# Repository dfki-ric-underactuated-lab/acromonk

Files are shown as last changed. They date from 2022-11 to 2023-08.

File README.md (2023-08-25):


<div align="center">

# AcroMonk: A Minimalist Underactuated Brachiating Robot
</div>

<div align="center">
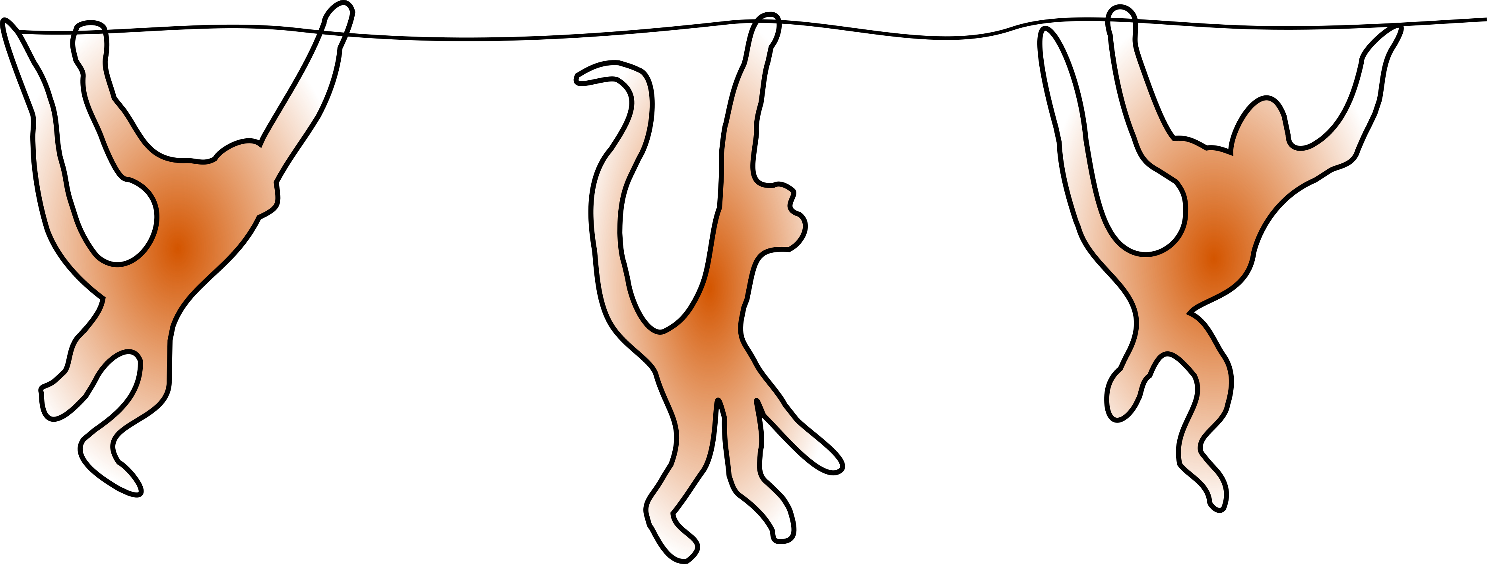
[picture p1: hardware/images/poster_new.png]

</div>

<div align="center">

</div>

## Description
This project offers an open-source and low-cost kit to test control algorithms
for underactuated robots.
it implements a **brachiation robot** platform called **AcroMonk** which
can brachiate robustly over a horizontally laid ladder bar. AcroMonk is
the simplest possible underactuated brachiator built using one quasi-direct
drive actuator (QDD) and passive grippers. This is the first brachiator with
unactuated grippers that can perform more than two brachiation maneuvers.
This project offers different control methods for trajectory stabilization
which can be studied using the kit. Additionally, it provides a list of
components, discusses best practices for implementation, and presents results
from experiments with the simulator and the real system. This repository
describes the hardware (CAD, Bill Of Materials ([BOM](hardware/bills-of-materials.md)) etc.) required to build
the physical system and provides the software (URDF models, simulation and controllers) to control it.

## Paper and Video References

The work is published in IEEE Robotics and Automation Letters 2023. The hardware experiment video of AcroMonk is also featured as an awesome robot video in [IEEE Spectrum Video Friday](https://spectrum.ieee.org/video-friday-acromonk).

Further links:
* Paper is available on [IEEE](https://ieeexplore.ieee.org/document/10106397) and [arXiv](https://arxiv.org/abs/2305.08373).
* Video is available on [youtube](https://youtu.be/FIcDNtJo9Jc).
## Documentation

The dynamics of the AcroMonk is explained [here](hardware/acrm-equations.md). Additionally, [mechatronics design](hardware/testbench-description.md), [behavior generation](software/python/simulation/behavior_generation/README.md) and [control](software/python/simulation/behavior_control/README.md) for the continuous brachiation are described in their respective readme files.

* [Mechatronics Design](hardware/testbench-description.md)
* [Behavior Generation](software/python/simulation/behavior_generation/README.md)
* [Behavior Control](software/python/simulation/behavior_control/README.md)
* [Software Guide](software/python/README.md)
* [Bill Of Materials (BOM)](hardware/bills-of-materials.md)

The CAD file is also provided on grabCAD.com. You can use the 3D viewer from their website to display the 3D model directly within your browser.
 - [Display AcroMonk in 3D](https://grabcad.com/library/acromonk-1)
## Authors #

* [Shivesh Kumar](https://robotik.dfki-bremen.de/en/about-us/staff/person/shku02) (Project Supervisor)
* [Mahdi Javadi](https://robotik.dfki-bremen.de/en/about-us/staff/person/maja04) (Hardware and Software Maintainer, Trajectory Optimization and Stabilization)
* [Daniel Harnack](https://robotik.dfki-bremen.de/en/about-us/staff/daha03.html) (Software Maintainer, Reinforcement Learning)
* [Shubham Vyas](https://robotik.dfki-bremen.de/en/about-us/staff/person/shvy01) (Trajectory Optimization, Hardware Concept)
* [Daniel Pizzutilo](https://robotik.dfki-bremen.de/de/ueber-uns/mitarbeiter/dapi01) (Mechatronics Design)
* Paula Stocco (Trajectory Optimization and Stabilization)

Feel free to contact us if you have questions about the test bench. Enjoy!

## Contributing

1. Fork it (<https://github.com/yourname/yourproject/fork>)
2. Create your feature branch (`git checkout -b feature/fooBar`)
3. Commit your changes (`git commit -am 'Add some fooBar'`)
4. Push to the branch (`git push origin feature/fooBar`)
5. Create a new Pull Request

## Safety Notes #

When working with a real system be careful and mind the following safety measures:

* Brushless motors can be very powerful, moving with tremendous force and speed. Always limit the range of motion, power, force and speed using configurable parameters, currently limited supplies, and mechanical design.

* The robot must be placed in a ladder bar cage and kept at least one-meter distance from the acromonk in case of operation.

* Make sure you have access to an emergency stop while doing experiments. Be extra careful while operating in the pure torque control loop.

* The robot is equipped with an onboard Lithium Polymer battery and needs proper care and attention. Make sure that you have all the necessary information for the LiPo batteries.

## Acknowledgments #
This work has been performed in the M-RoCK project funded by the
German Aerospace Center (DLR) with federal funds (Grant Number: FKZ 01IW21002)
from the Federal Ministry of Education and Research (BMBF) and is additionally
supported with project funds from the federal state of Bremen for setting up
the Underactuated Robotics Lab (Grant Number: 201-342-04-2/2021-4-1). The fourth author acknowledges support from the Stardust Reloaded project which has received funding from the European Union’s Horizon 2020 research and innovation program under the Marie Skłodowska-Curie grant agreement No 813644.
<div align="center">

</div>

## License

This work has been released under the BSD 3-Clause License. Details and terms of use are specified in the LICENSE file within this repository. Note that we do not publish third-party software, hence software packages from other developers are released under their very own terms and conditions, e.g. Stable baselines (MIT License) and Tensorflow (Apache License v2.0). If you install third-party software packages along with this repo ensure that you follow each individual license agreement.

## Citation

1. Javadi M., Harnack D., Stocco P., Kumar S., Vyas S., Pizzutilo D., Kirchner F., (2022). AcroMonk: A Minimalist Underactuated Brachiating Robot. In: IEEE Robotics and Automation Letters (RA-L), vol. 8, no. 6, pp. 3637-3644, June 2023, doi: 10.1109/LRA.2023.3269296.
```
@ARTICLE{10106397,
  author={Javadi, Mahdi and Harnack, Daniel and Stocco, Paula and Kumar, Shivesh and Vyas, Shubham and Pizzutilo, Daniel and Kirchner, Frank},
  journal={IEEE Robotics and Automation Letters}, 
  title={AcroMonk: A Minimalist Underactuated Brachiating Robot}, 
  year={2023},
  volume={8},
  number={6},
  pages={3637-3644},
  doi={10.1109/LRA.2023.3269296}}
```

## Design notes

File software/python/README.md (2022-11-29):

<div align="center">

# Software guide
</div>

This document provides instruction guides on executions of the software package in simulation and on the Raspberry Pi for real-time execution.

- [Simulation guide](simulation/README.md)
- [AcroMonk system guide](real_system/README.md)

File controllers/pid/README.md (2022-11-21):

#  Proportional–Integral–Derivative (PID) Control #

## Theory #

This controller is designed to follow a precomputed trajectory. Particulary, the controller can process trajectories that have been found with help of the [trajectory optimization](../../trajectory_optimization/direct_collocation/README.md). The torque processed by the PID control terms via:
```math
u(t) = K_p e(t) + K_i \int_0^t e(t') \text{d}t' + K_d \frac{\text{d}e(t)}{\text{d}t}
```
where $`e(t)`$ is the position error at timestep t. The values are assumed to be in SI units, i.e. time in s, position in rad, velocity in rad/s, torque in Nm.

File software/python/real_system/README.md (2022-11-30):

# Trajectory Stabilization with AcroMonk
The following instructions assume that the scripts will be executed on the Raspberry Pi. The required packages that need to be installed on the Raspberry Pi are provided in the [requirement.txt](requirements.txt).

A Makefile is provided in the following folder for the automatic execution of the robust forward brachiation using TVLQR and PD controller:

`software/python/real_system/Makefile`

The following parameters can be used for arbitrary behavior:

```
TEST          : stabilizing controller (pd, tvlqr), default=pd
FILE          : swing trajectory (BF trajectory in data/trajectories/closed_loop folder), default=BF_tvlqr.csv
MOTOR_ID      : mjbots servo id, default=7
BUS_NUMBER    : bus number on pi3hat, default=4
FILE_RECOVERY : recovery trajectory (Recovery trajectory in data/trajectories/closed_loop folder), default=ZF_tvlqr.csv
INIT_CONF     : initial configuration of the AcroMonk (1, 2), default=1: description provided in initial configuration section of this README
NBRACH        : number of brachiation maneuvers, default=1
```
for example:

```
make NBRACH=3  TEST=tvlqr
```
executes 3 brachiation motions with TVLQR stabilization. After typing the execution command on the terminal, the initialization of the parameters and IMU will be started. If it returns no error in the terminal, you need to type in `y` if ready for the execution on the real system. 
The plots and the csv file are saved in the `results/real_system` folder. 

## Initial configuration
The zero offset coordinate of the motor will be set when the motor is energized. It is of great importance that the energization takes place when the robot has a hanging arm and $\theta_2=0$. The following table provides an overview of the possible initialization of the robot for the execution of the script. The arm with the computing compartment, i.e. Raspberry Pi and IMU, is shown in `green`.
<div align="center">

|INIT_CONF=1|INIT_CONF=2|
|:--:|:--:|
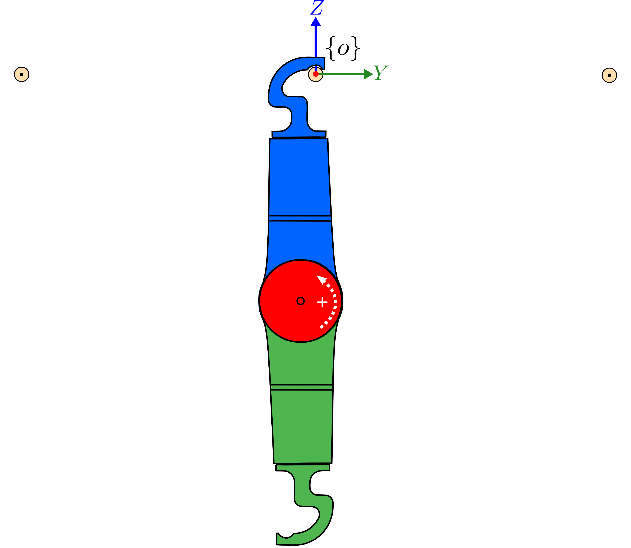
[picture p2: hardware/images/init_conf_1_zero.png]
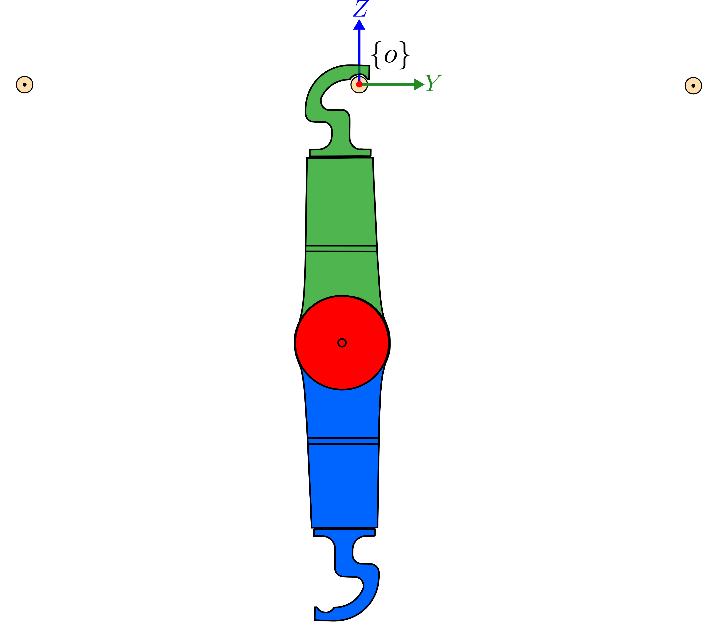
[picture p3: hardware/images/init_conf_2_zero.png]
|||
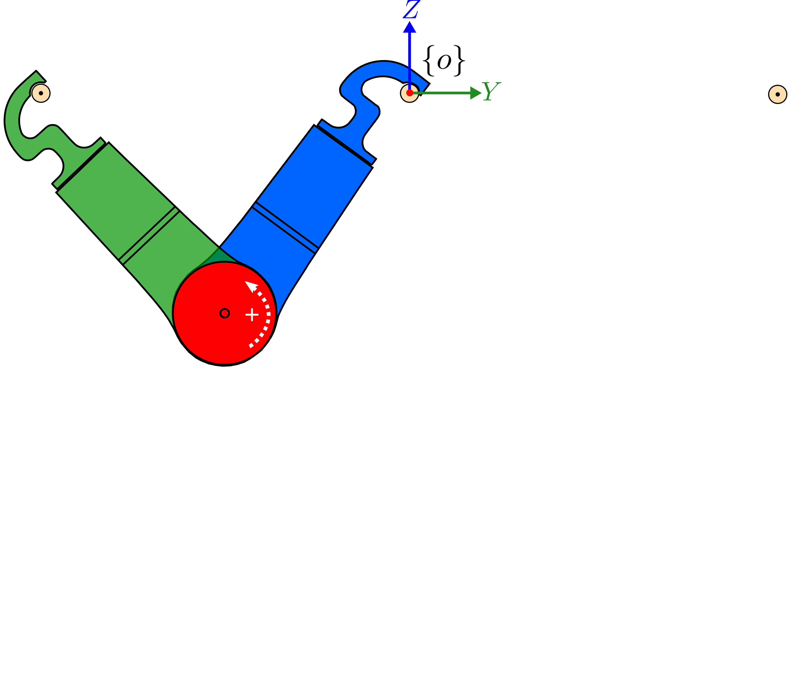
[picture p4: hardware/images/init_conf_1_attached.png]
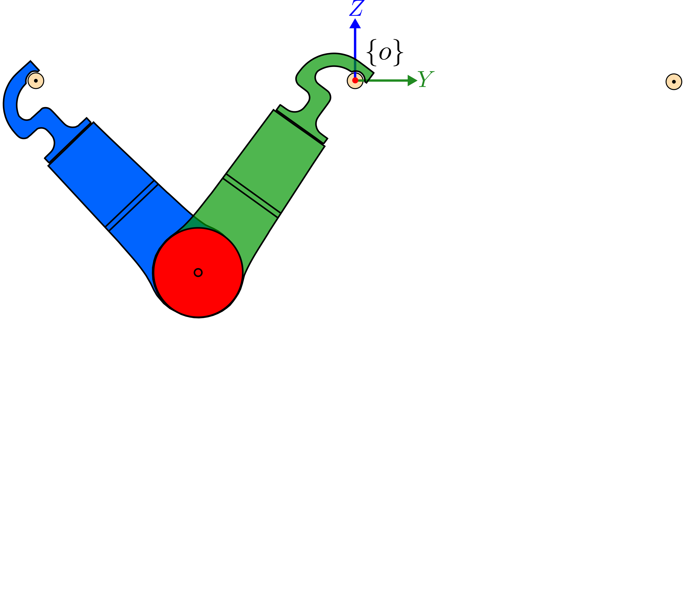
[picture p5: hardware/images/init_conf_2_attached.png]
|||

</div>
Here is the main difference between configurations:

- `INIT_CONF=1`: IMU swings with the arm and the motor axis is outward, i.e. positive rotation is counter-clockwise.
- `INIT_CONF=2`: IMU arm is attached to the bar and the motor axis is pointing towards the page, i.e. positive rotation is clockwise.

## Robust Forward Brachiation with AcroMonk
For the robust forward brachiation, if you start the script's execution with zero configuration and then press `y`, the state machine detects the hanging position of the arm and starts with the recovery mode `ZF` and further continues with the rest of the brachiation maneuvers. However, if you place the robot in `both arms attached` configuration after the initialization phase from zero configuration, and then press `y`, the execution will be started from the `BF` maneuver and continues with the brachiation.

## Atomic Behavior with AcroMonk
The following instructions allow the execution of the atomic behaviors `ZF, BF, ZB, FB` on the real system:
### BF
Place the robot in the initial position where both arms are attached to the bars and type one of the following commands depending on the `INIT_CONF`:
```
make 
```
or
```
make NBRACH=2 INIT_CONF=2
```

### ZF
Place the robot in the hanging configuration and type one of the following commands depending on the `INIT_CONF`:
```
make
```
or
```
make NBRACH=2 INIT_CONF=2
```

### ZB
Place the robot in the hanging configuration and type one of the following commands depending on the `INIT_CONF`:
```
make FILE_RECOVERY=ZB_pd.csv
```
or
```
make NBRACH=2 INIT_CONF=2 FILE_RECOVERY=ZB_pd.csv
```

### FB
To execute the FB maneuver, you need to execute the script in the following folder `software/python/real_system/FB_PD/tests/FB_brachiation.py`.

**Notes and cautions**

- This script works only with the `INIT_CONF=1`
- The following steps need to be taken for the real system test:
    - Place the robot in the hanging zero configuration 
    - Type in the terminal: ```sudo -E python3 FB_brachiation.py``` and if it returns no error, type in `y` and press `Enter`
    - The script waits for 10 seconds to let the operator attach the IMU arm to the front bar

## Forward Brachiation using Reinforcement Learning
A [guide](BF_Reinforcement_Learning/README.md) is provided for the execution of the Reinforcement learning algorithm on the AcroMonk.

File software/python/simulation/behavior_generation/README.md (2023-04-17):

<div align="center">

# Behavior Generation
</div>
Considering three fixed points for the robot as the following:

- Z (single support, hanging)
- B (double support with backward bar)
- F (double support with forward bar).

## Atomic Behaviors
Inspired by the typical brachiation of a monkey, the following four atomic behaviors can give rise to robust bidirectional brachiation over horizontal bars. Because of the passive gripper choice, additional behaviors have to be considered to release the swing arm from a bar, which is denoted as Back Release (BR) and Front Release (FR) to initiate a BF or FB atomic behavior, respectively. More info on the gripper's heuristics can be found [here](../../../../hardware/gripper-heuristics.md).

<div align="center">
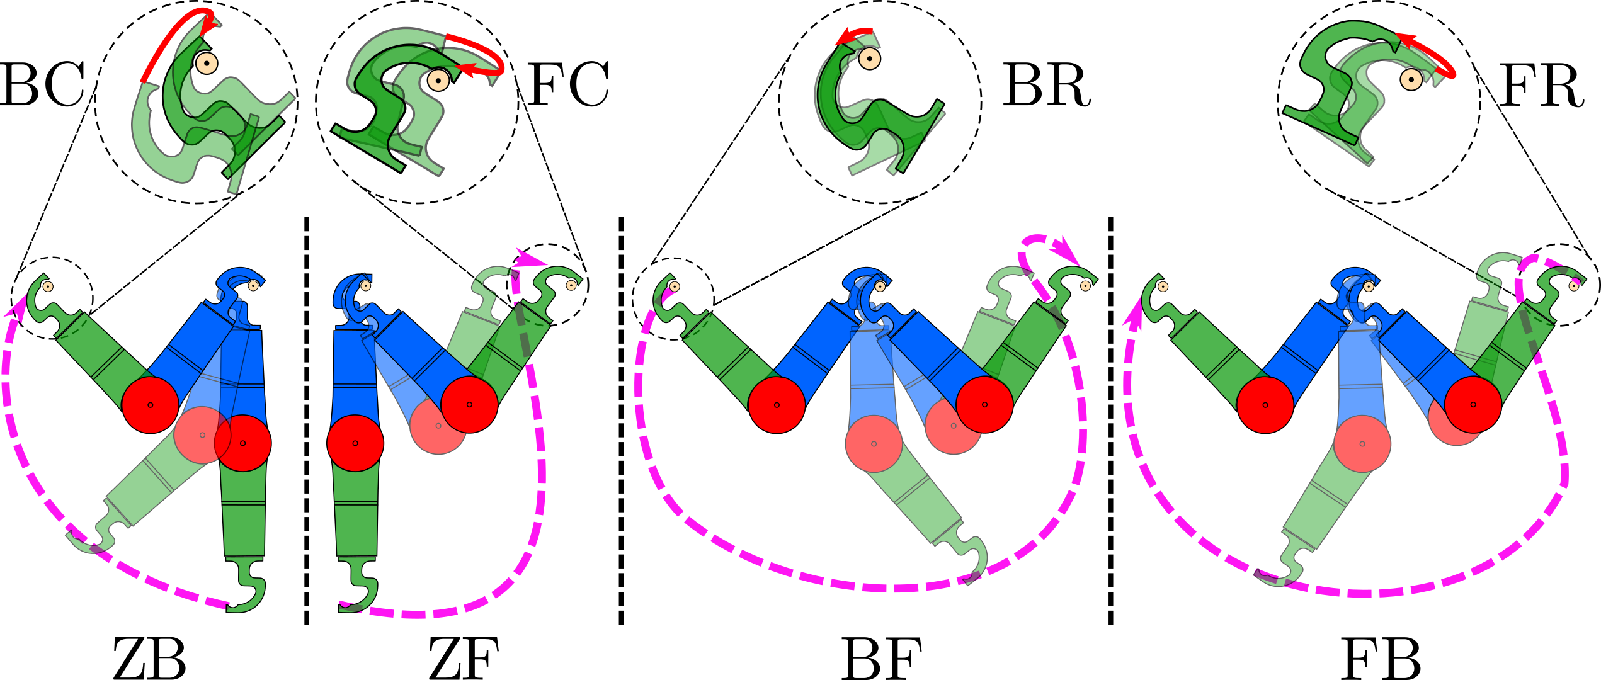
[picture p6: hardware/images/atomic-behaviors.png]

</div>

<div align="center">
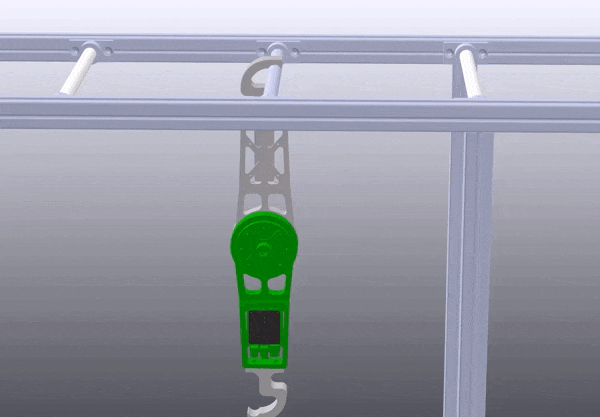
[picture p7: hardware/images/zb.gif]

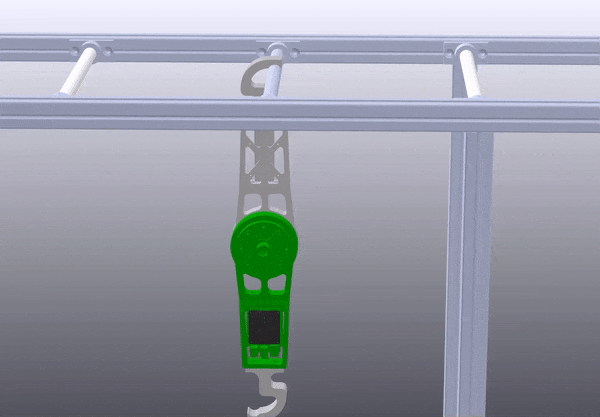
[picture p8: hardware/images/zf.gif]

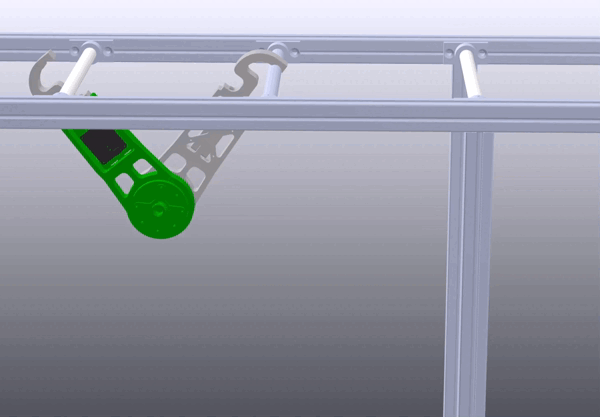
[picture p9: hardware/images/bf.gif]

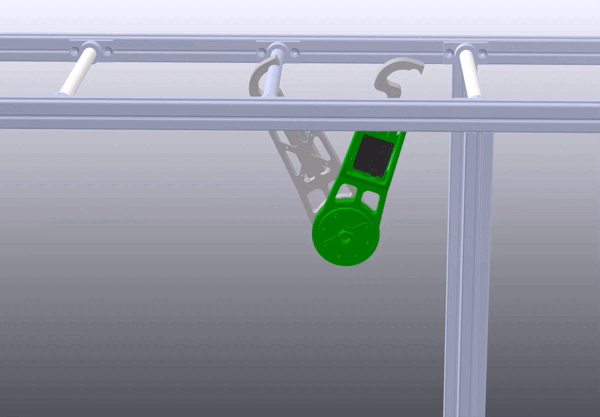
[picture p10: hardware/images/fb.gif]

</div>

## AcroMonk's Configuration for Atomic Behaviors
The unique gripper design offers a large region of attraction, shown in orange color, for grasping a target bar and a well-defined pivot point for the swing maneuvers. The passive gripper imposes a constraint on grasping configuration, which plays a vital role in the robot's final configuration. 
<div align="center">
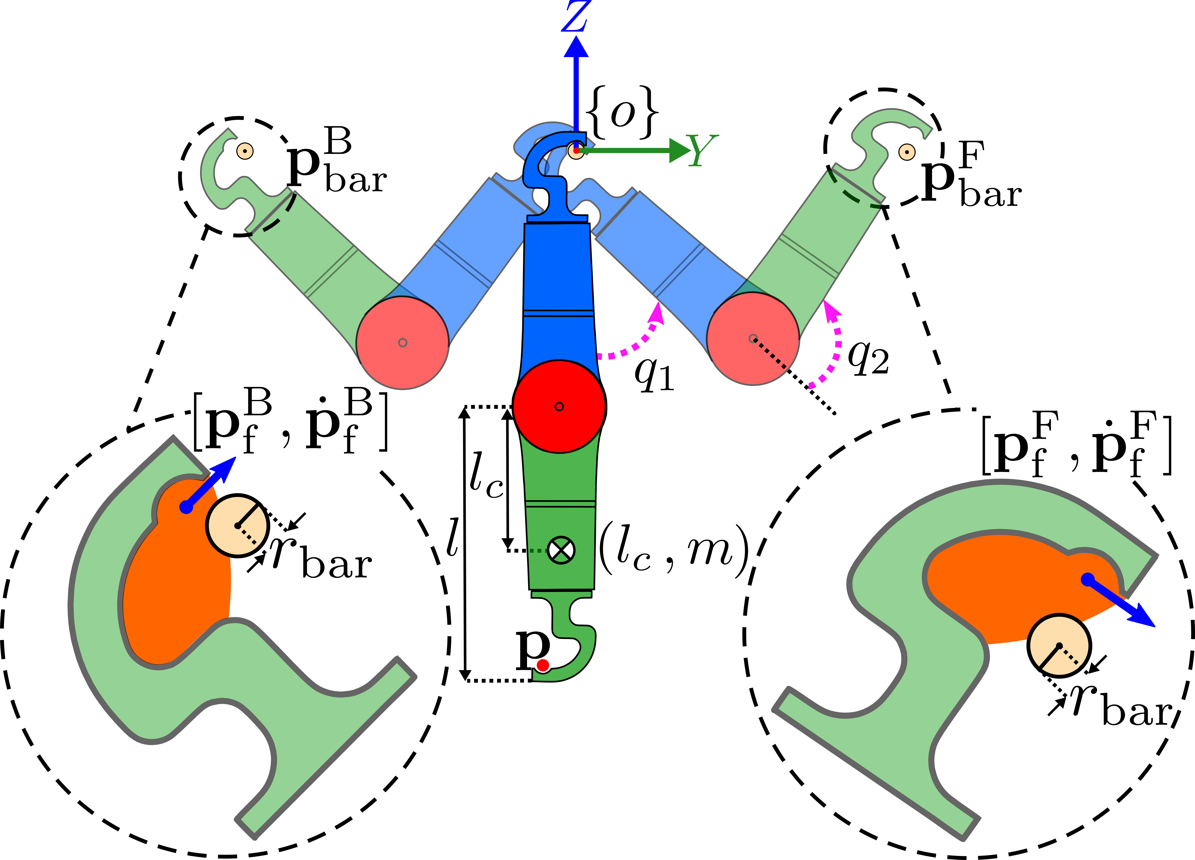
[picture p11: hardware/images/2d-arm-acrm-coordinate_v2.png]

</div>

## Behavior Generation Methods

The atomic behaviors are generated using the following methods:
- Trajectory Optimization with [Direct Collocation](trajectory_optimization/direct_collocation/README.md) (ZF, ZB, FB, BF)
- [Reinforcement Learning](reinforcement_learning/README.md) (BF)

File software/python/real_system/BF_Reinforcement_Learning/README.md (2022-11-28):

run rl controller on the real robot from here with

    python mutliple_BFs.py rl {bus_number} {motor_id}

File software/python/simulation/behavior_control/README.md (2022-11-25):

<div align="center">

# Behavior Control
</div>

The optimal behaviors generated by the trajectory optimization methods need to be tracked and stabilized. 
The following controllers are used for trajectory stabilization purposes:
- Model-based
    - [Time-Varying Linear Quadratic Regulator (TVLQR)](controllers/tvlqr/README.md)
- Model-free
    - [Proportional-Integral-Derivative (PID) control](controllers/pid/README.md)

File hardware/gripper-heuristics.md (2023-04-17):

<div align="center">

# Gripper Heuristics
</div>

The passive gripper design was empirically optimized such that the gripper’s interactions with the monkey bars can be achieved with a control heuristic on the elbow motor, which depends on contact friction characteristics and the values may vary with other setups. The counter-clockwise rotation of the motor is referenced as positive. 

<div align="center">

</div>

## Release
To simplify the control, Back-to-Front (BF) and Front-to-Back (FB) controllers are only engaged once the swing arm releases the bar. 

### Back Release
Empirical state data $x = [q, q̇]^T$ was collected over $20$ trials at the point of controller transition and the results are depicted in the following Figure. 
<div align="center">
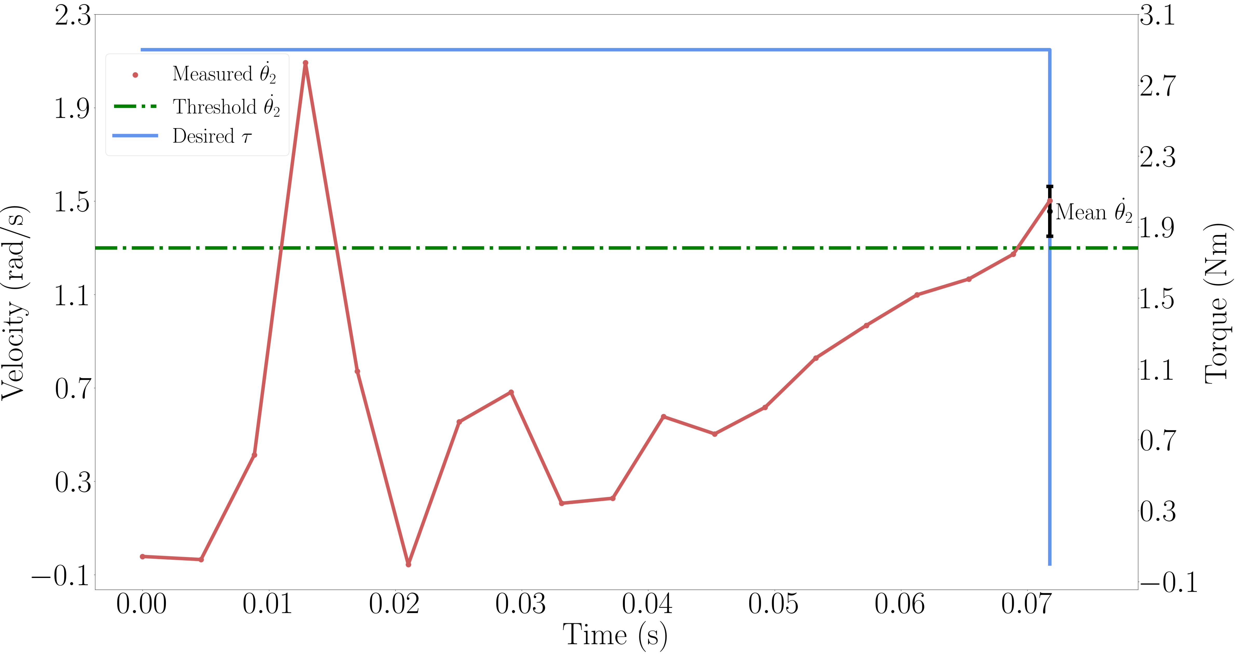
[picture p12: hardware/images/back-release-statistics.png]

</div>

Despite not releasing the hook, a peak in the velocity measurement is observed around $0.015$ seconds when a constant torque is applied. Therefore a conservative duration of $0.05$ seconds is chosen to avoid the misinterpreting of the velocity readings.
Observations show that it is possible to achieve a robust release even with a torque of $2.5\ \text{Nm}$ for $0.34\ \text{m}$ bar distance, which is lower than the $2.9\ \text{Nm}$ depicted in Figure. After this, if the elbow velocity surpasses $1.45\ \text{rad/s}$, the controller switches to BF brachiation. 

### Front Release
For FB swing, which starts with Front Release (FR), a constant torque approach was insufficient due to the different contact angles of the hook on the bar. In order to clear the front bar, an initial high negative torque and a subsequent lower sustained positive torque is applied to lift the hook groove off the bar. Similar to BR, state data was collected at this transition point.
## Catch

The catch behavior is executed at the end of each atomic sub-behavior during continuous brachiation to provide a defined rotation point for the next brachiation. This is realized by applying a negative torque for $0.1$ seconds with a magnitude of $0.8\ \text{Nm}$ . Duration and magnitude were chosen empirically such that the bar slides into the groove if the hook is slightly misplaced, but no movement is caused if the bar is already resting in the groove.

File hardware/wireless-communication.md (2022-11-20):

This is a guide provides information on how to setup the Raspberry pi 4 and access to the AcroMonk remotely. 

## Setup Raspberry Pi
Here is [a useful guide](https://projects.raspberrypi.org/en/projects/raspberry-pi-setting-up) how to setup a Raspberry Pi.

## Remote Access
In the follwing, the steps that needs to be taken to access the onboard Raspberry Pi are listed.
### Wireless connection
In order to access the robot remotely, one of the following strategies can be followed:
- Setup the Raspberry pi as a wireless access point ([link](https://raspberrypi-guide.github.io/networking/create-wireless-access-point))
- Setup a router and connect the Raspberry Pi and server to the same router
### Obtain the IP address
To get the IP adderss you need to open a terminal in your Raspberry Pi OS use the following command:
```
hostname -I
```
### Enable SSH
One way to enable the SSH is to use the following command in **terminal**:
```
sudo raspi-config
```
select the `interfacing Options`. Navigate to and select `SSH`. Choose `Yes`. Select `OK`. Choose `Finish`.

### Access via SSH

Using the IP address that is obtained in the previous step, one can connect to Raspberry pi by typing the following command in terminal:

```
ssh pi@<IP>
```

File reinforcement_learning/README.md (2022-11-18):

# Reinforcement Learning
## Installation
This installation instruction assumes Ubuntu 20.04. 
We recommend using a dedicated python virtual environment, e.g. using 

    python3 -m venv path/to/your/new/venv

The training and simulation environment uses Mujoco 2.1, which has to be installed first. In order to easily 
find the package, you can add 

    export LD_LIBRARY_PATH=$LD_LIBRARY_PATH:/path/to/mujoco/folder/bin

to your .bashrc. The path is ~/.mujoco/mujoco210/bin by default (see https://github.com/openai/mujoco-py 
for more instructions). 

The requirements can be installed from the file located in 
reinforcement_learning/requirements.txt (e.g. 
<code>pip install -r requirements.txt</code>)

Hint: if you face an 

    GLEW intialization error: Missing GL version

adding 

    export LD_PRELOAD=$LD_PRELOAD:/usr/lib/x86_64-linux-gnu/libGLEW.so

to .bashrc can help.

To simulate the trained rl controller, move to the /scripts 
folder and run <code>python replay_rl_model.py</code>. The result should be something like this:

<div align="center">

</div>

## Training
Training a new controller is done via

    python scripts/train_rl_model.py

The parameters for training and simulation will be loaded from 
the parameters.json file in /training. The reward function 
is modified by changing the weights in parameters.json under the 
"reward_setup" keyword. Rewards with a weight of 0 do not 
take effect. The reward "reward_name" expects a method 
"_reward_reward_name" of evironment/acromonk, so if you want to 
define a new reward, you have to set the weight in the parameters
file and implement the respective method in the acromonk 
environment. 

The current (dense) reward setup looks like this:

<div align="center">
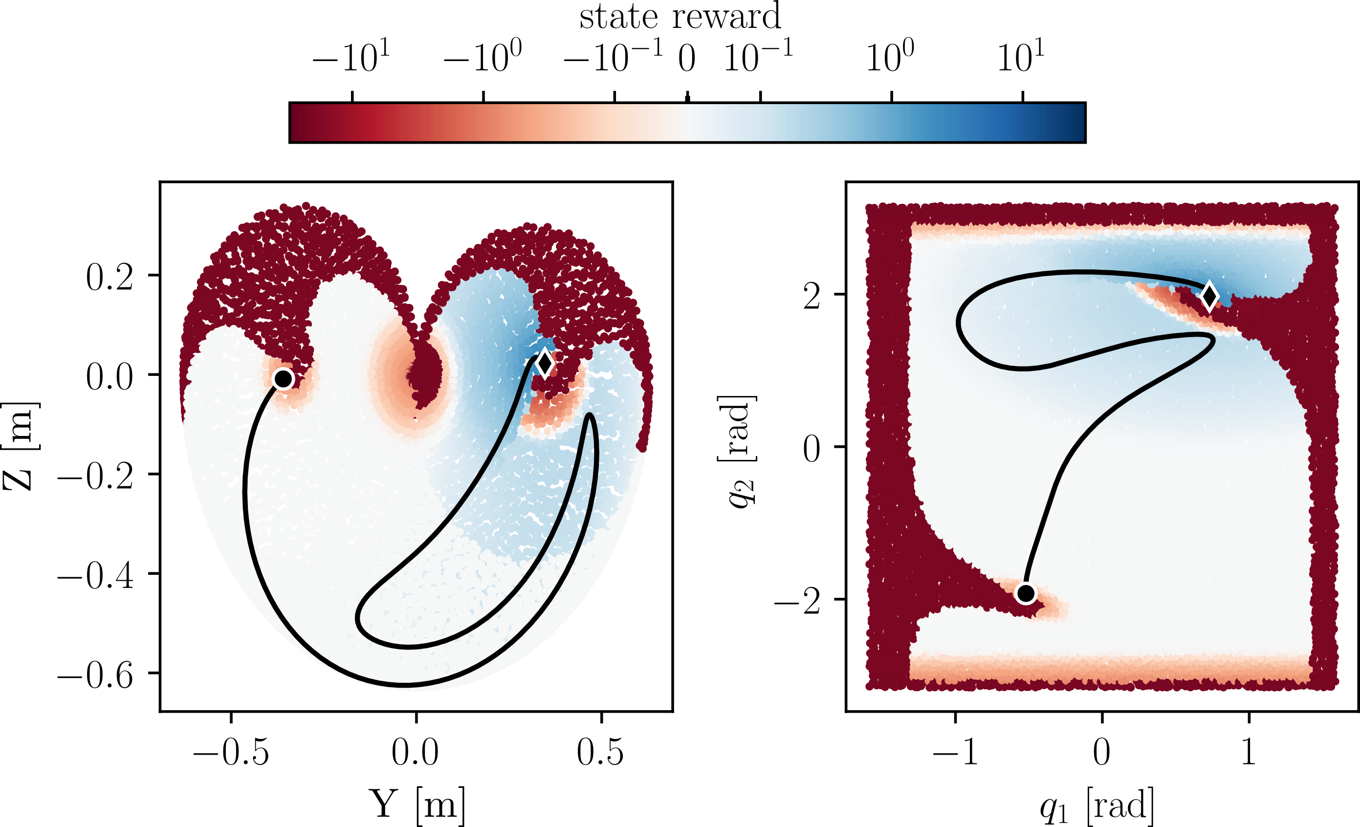
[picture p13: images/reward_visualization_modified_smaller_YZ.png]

</div>

The trained controller will be saved in 
../data/trained_controllers under a folder with 
the current time, along with a copy of the used 
parameters for reproducibility. You can visualize your trained 
controller by changing the path in scripts/replay_rl_model.py in line 15. 
A specific checkpoint can be chosen by the evaluation 
steps, e.g. 
<code>rl_checkpoint = '10000'</code>. 
(default 'best' uses the best performing agent). 

---
**Challenges:**
- Can you train a controller that achieves BF brachiation in one swing?
- Can you train a BF controller only using enegy based reward?
- Can you train a BF controller only using sparse rewards?
- Can you train controllers for the other atomic behaviors FB/ZB/ZF ?
---

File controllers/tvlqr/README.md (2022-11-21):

#  Time-varying Linear Quadrativ Regulator (TVLQR)

## Theory

This controller is designed to follow a precomputed trajectory. Particulary, the controller can process trajectories that have been found with help of the [trajectory optimization](../../trajectory_optimization/direct_collocation/README.md). 

The Time-varying Linear Quadratic Regulator (TVLQR) is an extension to the regular [LQR controller](https://underactuated.csail.mit.edu/lqr.html).
The TVLQR controller tries to stabilize the system along a nominal trajectory. For this, at every timestep the system dynamics are linearized around the state of the nominal trajectory $`\mathbf{x}_0(t), \mathbf{u}_0(t)`$ at the given timestep $`t`$ as:

```math
\begin{equation*}
\dot{\mathbf{x}} =  \mathbf{A}(t)\mathbf{x} + \mathbf{B}(t)\mathbf{u}
\end{equation*}
```

The LQR formalism then can be used to derive the optimal controller at timestep $`t`$:
```math
\begin{equation*}
u(\mathbf{x}) = \mathbf{u}_0(t) - \mathbf{K}(t) \left( \mathbf{x} - \mathbf{x}_0(t)\right)
\end{equation*}
```

For further reading, we recommend chapter 8 of this [Underactuated Robotics [1]](http://underactuated.mit.edu/) lecture.

## Dependencies

The trajectory optimization using direct collocation and TVLQR gains are obtained by taking advantage of [Drake toolbox [3]](https://drake.mit.edu/).

## References

[[1] Russ Tedrake. Underactuated Robotics: Algorithms for Walking, Running, Swimming, Flying, and Manipulation (Course Notes for MIT 6.832).](http://underactuated.mit.edu/)

[[2] Model-Based Design and Verification for Robotics](https://drake.mit.edu/).

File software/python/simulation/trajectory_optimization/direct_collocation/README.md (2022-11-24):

# Trajectory optimization using direct collocation

## Theory

Direct collocation is an approach from ***collocation methods*** , which transforms the optimal control problem into a mathematical programming problem. The numerical solution can be achieved directly by solving the new problem using sequential quadratic programming [[1]](https://arc.aiaa.org/doi/pdf/10.2514/3.20223)[[2]](http://underactuated.mit.edu/trajopt.html).

## Atomic behaviors
Considering three fixed points for the robot as the following:
- Z (single support, hanging)
- B (double support with backward bar)
- F (double support with forward bar)

the following figure depicts the general possibilities for the robot's motion.

<div align="center">

</div>

<div align="center">




</div>

## AcroMonk's Configuration for Atomic Behaviors
The unique gripper design offers a large region of attraction, shown in orange color, for grasping a target bar and a well defined pivot point for the swing maneuvers. The passive gripper impose a constraint on grasping configuration, which plays a vital role in robot's final configuration. 
<div align="center">

</div>

## Formulation

The continuous time trajectory optimization problem of the AcroMonk is shown in the following:
```math
\begin{align*}
		&\min_{\mathbf{x}, u} W T + \int_{0}^{T} \left(\mathbf{x}^T \mathbf{Q} \mathbf{x} + u^T R u\right) dt  \\
		&\mathrm{subject\ to}:\\
	    &\dot{\mathbf{x}} = \mathbf{f}(\mathbf{x}, u)\\
	    &|\mathbf{x}| \leq \mathbf{x}_\text{lim}, \ \ |u| \leq u_\text{lim}\\
	    &\mathbf{x}(0) = \mathbf{x}_0, \ \ \ \mathbf{x}(T) = \mathbf{x}_f\\
	    &|| \mathbf{p} - \mathbf{p}^\text{F}_\text{bar} || > r_\text{bar}, \ \  || \mathbf{p} - \mathbf{p}^\text{B}_\text{bar} || > r_\text{bar}
\end{align*}
```

- $`{\bf{x}} = {{[\theta_1(.), \theta_2(.), \dot{\theta_1}(.), \dot{\theta_2}(.)]}}^T`$: Angular positions and velocities are the states of the system 

- $`u`$: Input torque of the system applied by motor

- $`{\bf{x}}_0:`$ Initial state constraint

- $`{\bf{x}}_F:`$ Terminal state constraint

- $`|| \mathbf{p} - \mathbf{p}^\text{F}_\text{bar} || > r_\text{bar}, \ \  || \mathbf{p} - \mathbf{p}^\text{B}_\text{bar} || > r_\text{bar}`$: Collision avoidance with bars

- $`WT`$: Final cost to minimize total trajectory time $`T`$ with weight $`W`$ 

- $`\mathbf{x}^T \mathbf{Q} \mathbf{x}`$: State regularization cost with $`\mathbf{Q}=\mathbf{Q}^T \succeq 0`$ as state regulization term

- $`l(u) = u^TR u`$: Running cost with $`R`$ as input weight

- $`\mathbf{f}(\mathbf{x}, u)`$: [Nonlinear dynamics of the AcroMonk](../../../../../hardware/acrm-equations.md) considered as equality constraint

## Dependencies

The trajectory optimization using direct collocation for all the atomic behaviors is accomplished by taking advantage of [Drake toolbox [3]](https://drake.mit.edu/).

## References
[[1] Hargraves, Charles R., and Stephen W. Paris. "Direct trajectory optimization using nonlinear programming and collocation." Journal of guidance, control, and dynamics 10.4 (1987): 338-342](https://arc.aiaa.org/doi/pdf/10.2514/3.20223)

[[2] Russ Tedrake. Underactuated Robotics: Algorithms for Walking, Running, Swimming, Flying, and Manipulation (Course Notes for MIT 6.832).](http://underactuated.mit.edu/)

[[3] Model-Based Design and Verification for Robotics](https://drake.mit.edu/).

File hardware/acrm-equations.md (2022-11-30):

<div align="center">

# AcroMonk
</div>

<div align="center">
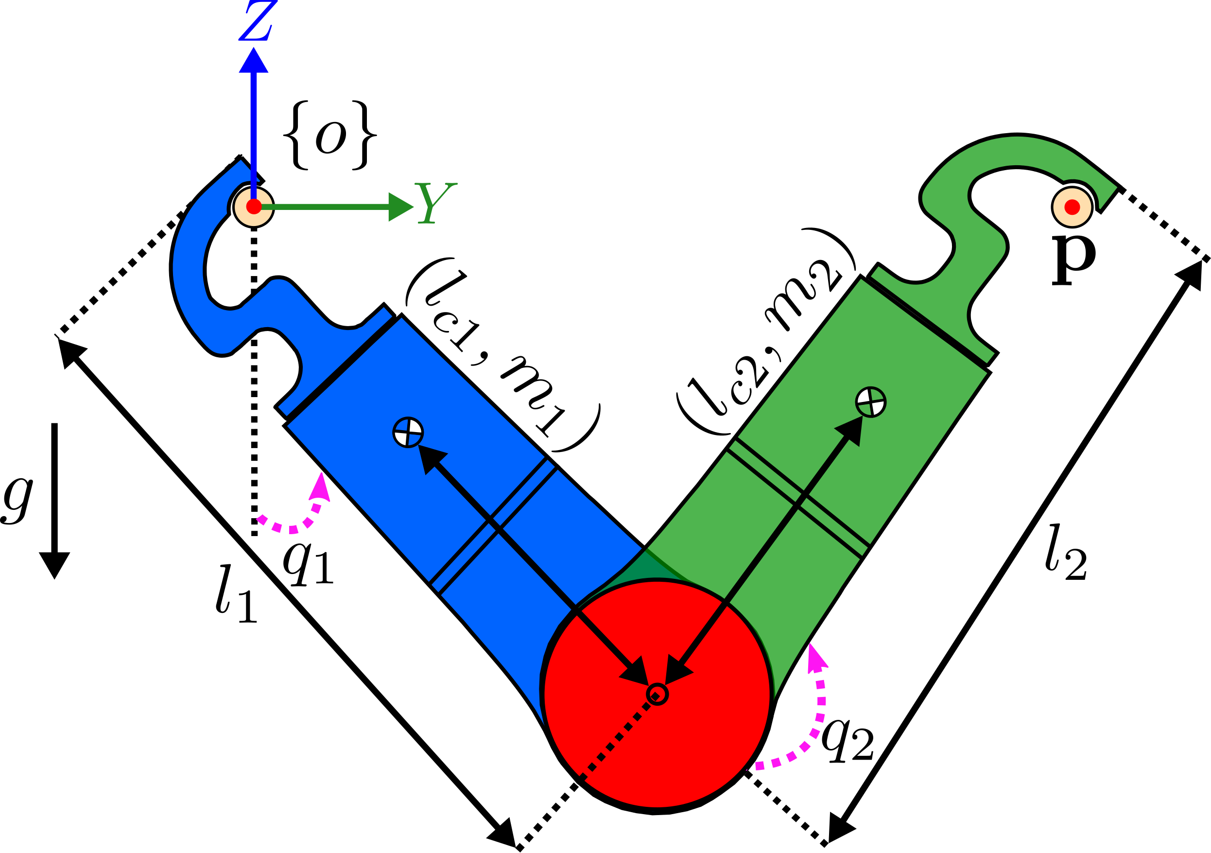
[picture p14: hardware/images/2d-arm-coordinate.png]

</div>

## Equation of Motion
The general formulation for equation of motion is shown in the following:

```math
\begin{equation*}
	\mathbf{M}(\mathbf{q}) \ddot{\mathbf{q}} +\mathbf{C}(\mathbf{q}, \dot{\mathbf{q}}) = \mathbf{\tau}_g (\mathbf{q}) + \mathbf{B} u
\end{equation*} 
```
The mass-inertia matrix $\mathbf{M}$ for AcroMonk is
```math
\begin{equation*} 
	\mathbf{M}(\mathbf{q}) = 
	\begin{bmatrix} I_1 + I_2 + m_2 l_1^2 +
      2m_2 l_1 l_{c2} c_2 & I_2 + m_2 l_1 l_{c2} c_2 \\ I_2 + m_2 l_1 l_{c2} c_2
      & I_2 
      \end{bmatrix}
\end{equation*}
```
with the shorthand notation $s_1 = \sin(q_1), c_1 = \cos(q_1)$. 
Accordingly, Coriolis matrix is:
```math
\begin{equation*}
	\mathbf{C}(\mathbf{q},\dot{\mathbf{q}}) =
	\begin{bmatrix} 
		-2 m_2 l_1 l_{c2} s_2 \dot{q}_2 & -m_2 l_1 l_{c2} s_2
		\dot{q}_2 \\ 
		m_2 l_1 l_{c2} s_2 \dot{q}_1 & 0 
	\end{bmatrix}
\end{equation*}
```

with the gravity vector as:

```math
\begin{equation*}
      \mathbf{\tau}_g(\mathbf{q}) = 
      \begin{bmatrix} 
	      -m_1 g l_{c1}s_1 - m_2 g (l_1 s_1 + l_{c2}s_{1+2}) \\ 
	      -m_2 g l_{c2} s_{1+2} 
      \end{bmatrix}
 \end{equation*}
```

and the actuation matrix is $\mathbf{B} = [0 \quad 1]^T$, which captures the underactuation of the system.

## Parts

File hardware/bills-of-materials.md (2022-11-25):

<div align="center">

# Bill of Materials
</div>
This document provides the bill of materials that is used for the AcroMonk testbench. 

|Material|Price in Germany (Euro)|Sample Provider|
|:--|:--:|:--:|
|LiPo Battery|27.80|[purchase link](https://www.stefansliposhop.de/akkus/sls-xtron/sls-xtron-30c/sls-xtron-1200mah-6s1p-22-2v-30c-60c::1225.html)|
|Raspberry Pi 4 Modell B 4 GB|81.48|[purchase link](https://www.rasppishop.de/Raspberry-Pi-4-Modell-B-4GB-SDRAM)|
|MicroSD 64GB|12.49|[purchase link](https://www.rasppishop.de/Sandisk-microSDHC-UHS-I-64GB-Class10-mit-Raspberry-Pi-OS)|
|qdd100 beta 3 servo|539.00 \$|[purchase link](https://mjbots.com/collections/servos-and-controllers/products/qdd100-beta-3)|
|mjbots pi3hat|149.00 \$|[purchase link](https://mjbots.com/products/mjbots-pi3hat-r4-4b)|\
|Reely joystick|73.99|[purchase link](https://www.conrad.de/de/p/reely-ht-6-hand-fernsteuerung-2-4-ghz-anzahl-kanaele-6-inkl-empfaenger-1310037.html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)|
|Step-Down Voltage Regulator|4.90|[purchase link](https://www.fpv24.com/en/iflight/iflight-5v12v-step-down-voltage-regulator-2-8s-micro-bec)|
|24V DC Relay|5.99|[purchase link](https://www.conrad.com/p/song-chuan-896h-1ch-c1-24v-dc-automotive-relay-24-v-dc-20-a-1-change-over-504154)|
|Electonic switch 30A|23.99|[purchase link](https://www.amazon.de/Dilwe-Elektrischer-Schalter-Fernbedienung-Ersatzteil/dp/B07R1VGSNN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)|
|BASF Ultrafuse PLA|26.99|[purchase link](https://www.conrad.de/de/p/basf-ultrafuse-pla-0002a075-pla-black-filament-pla-1-75-mm-750-g-schwarz-1-st-1417247.html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)|
|Screws, nuts, bolts|10|--|
|Resistor, varistor and cables|10|--|
|3D printing cost|--|--|
|Total estimated cost|950-1000|

## Notes
* The underactuated lab does not have any relation with the providers and does not accept any responsibility for any possible issues with the third parties. 
* The shipping and 3D printing expenses are excluded from the total cost.

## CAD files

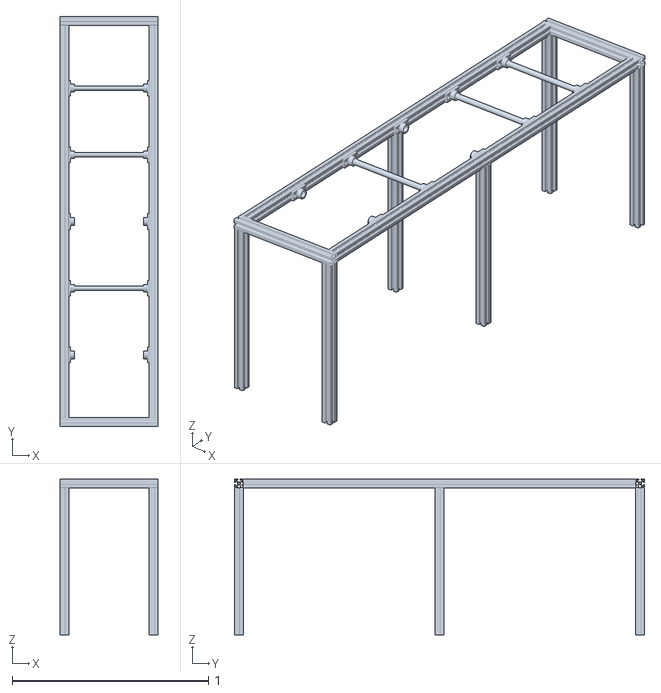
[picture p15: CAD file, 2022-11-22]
data/simulation_models/meshes/Base.obj
0.5 x 2.09 x 0.795

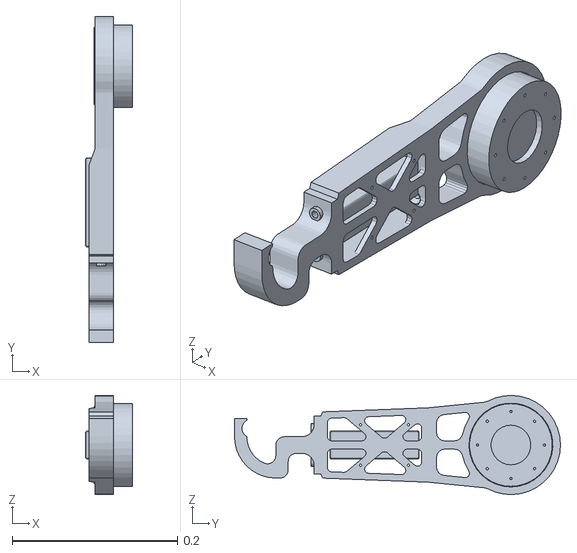
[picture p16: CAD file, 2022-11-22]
data/simulation_models/meshes/hook_1.obj
0.0567 x 0.395 x 0.12

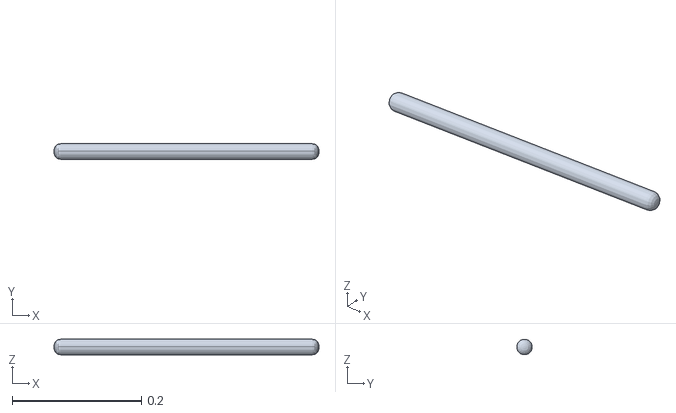
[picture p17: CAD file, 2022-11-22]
data/simulation_models/meshes/stick_1.obj
0.41 x 0.024 x 0.024

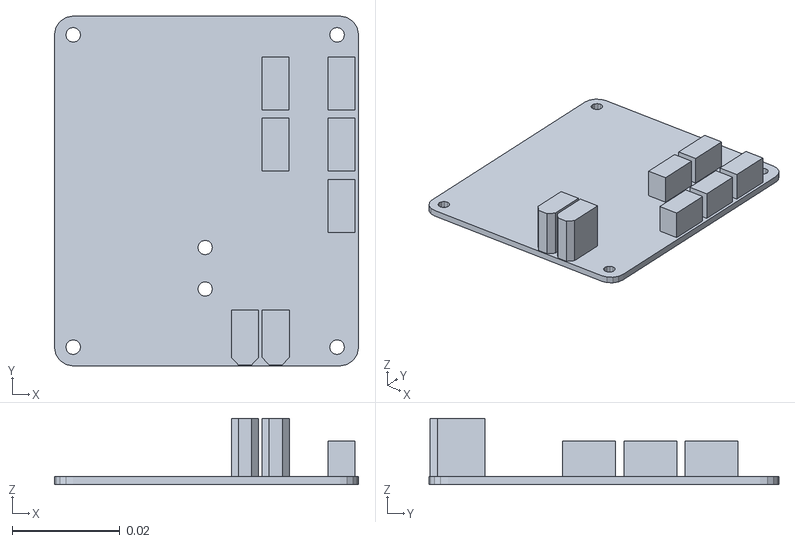
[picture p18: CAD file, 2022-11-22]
data/simulation_models/meshes/IMU.obj
0.0565 x 0.065 x 0.0123

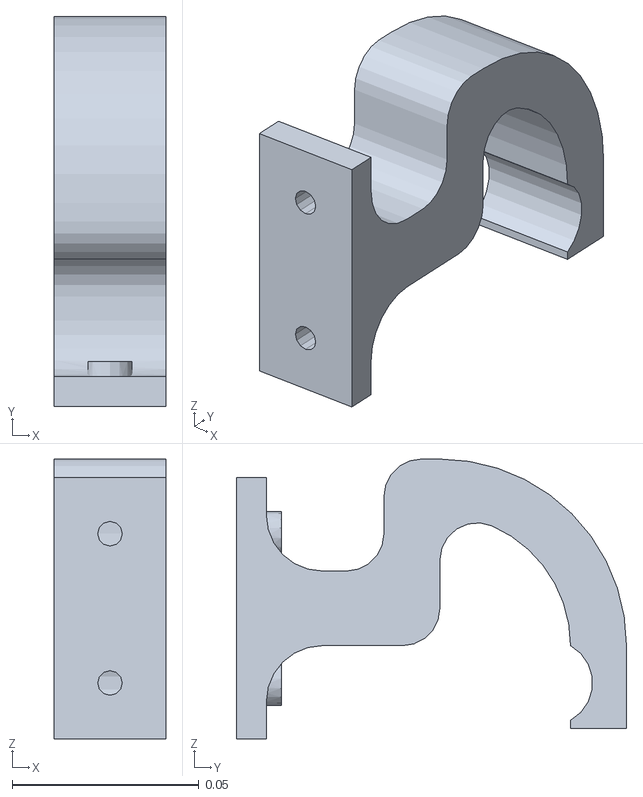
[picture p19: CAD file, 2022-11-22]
data/simulation_models/meshes/hook_2.obj
0.03 x 0.105 x 0.075

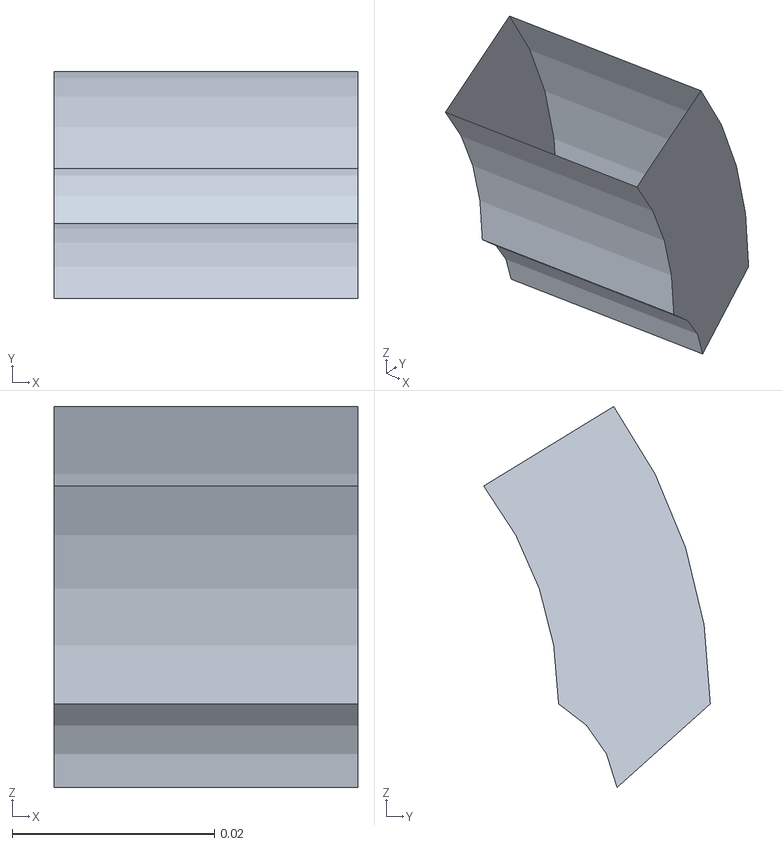
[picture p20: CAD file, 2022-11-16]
data/simulation_models/meshes/hook_2_upper_lower.STL
0.03 x 0.0224 x 0.0377

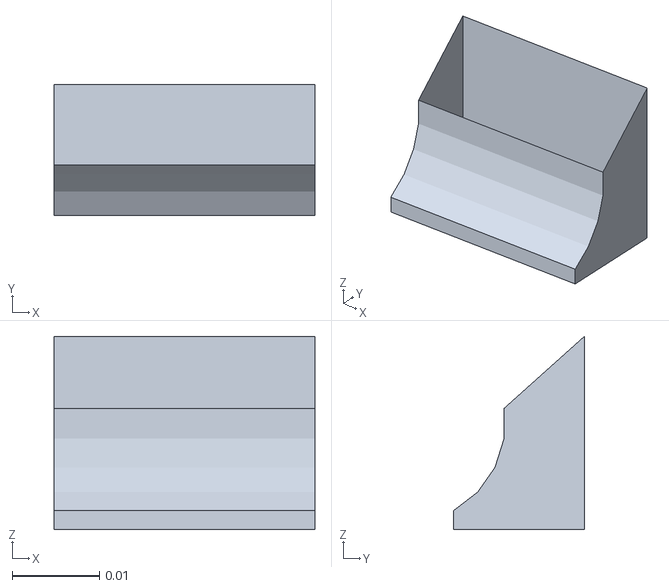
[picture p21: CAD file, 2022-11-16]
data/simulation_models/meshes/hook_2_upper_tip.STL
0.03 x 0.015 x 0.0222

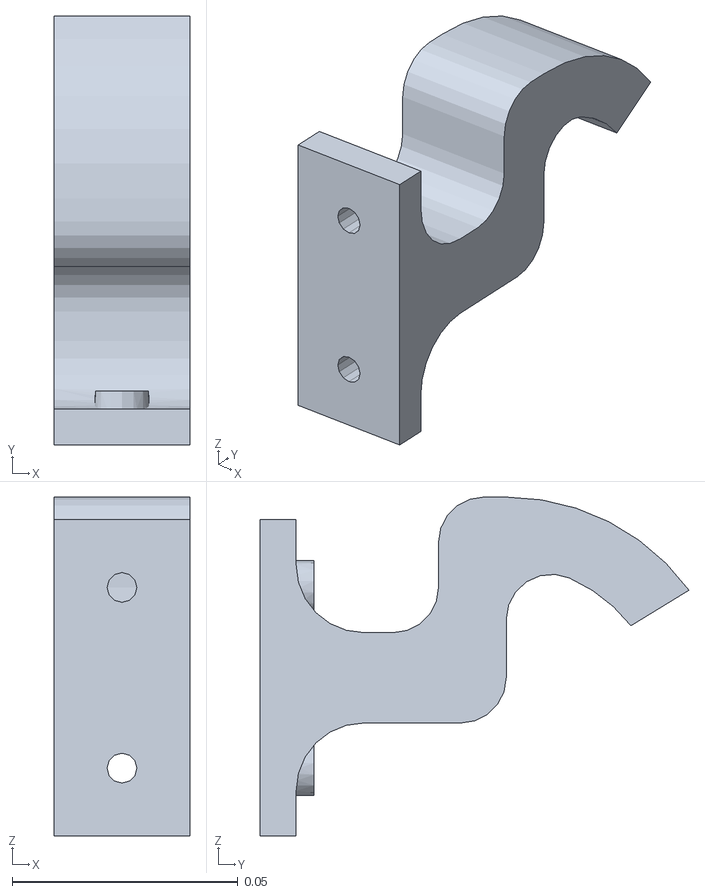
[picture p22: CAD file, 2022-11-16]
data/simulation_models/meshes/hook_2_lower.STL
0.03 x 0.095 x 0.075

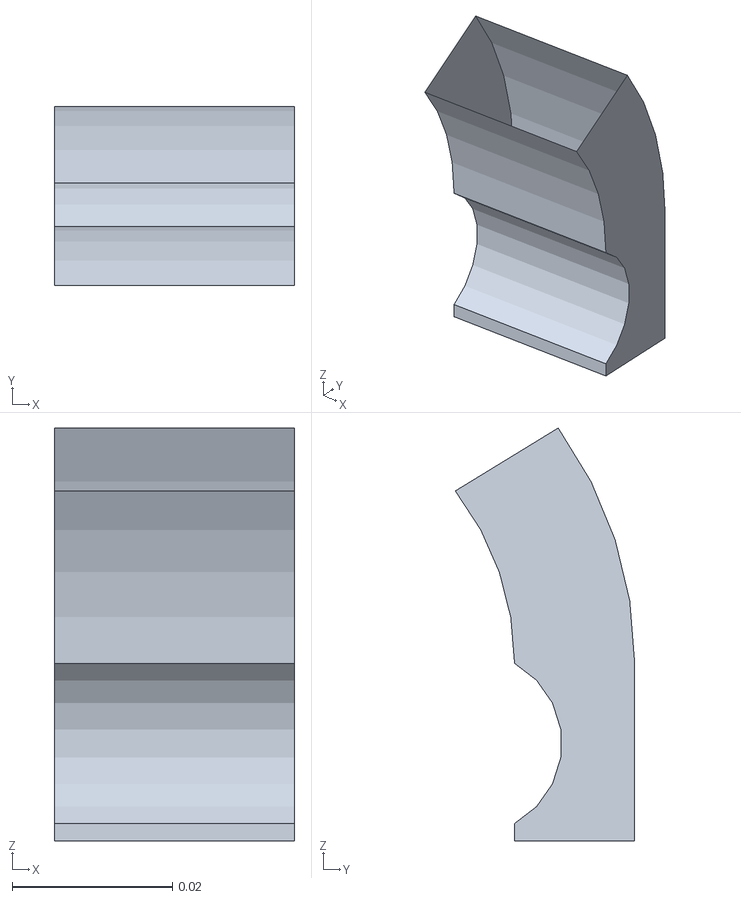
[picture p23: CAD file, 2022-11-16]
data/simulation_models/meshes/hook_2_upper.STL
0.03 x 0.0224 x 0.0516

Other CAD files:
data/simulation_models/meshes/stick_2.obj

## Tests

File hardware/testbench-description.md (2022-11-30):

<div align="center" >

# Mechatronics Design
</div>

## Mechanics
The main idea for the design of the AcroMonk is to have a portable and robust agile robot with a minimum effort for the modification. 
A modular design is proposed that uses 3D printing technology for ease of reproducibility. 
Overall, the structure consists of six unique 3D-printed parts highlighted with different colors that are connected by screw-nut fasteners for easy assembly, with compartments for electronics, a battery, counterweights, and cable guides. The innovative gripper design of the AcroMonk makes him the first brachiator that can brachiate continuously with the passive gripper.

<div align="center">
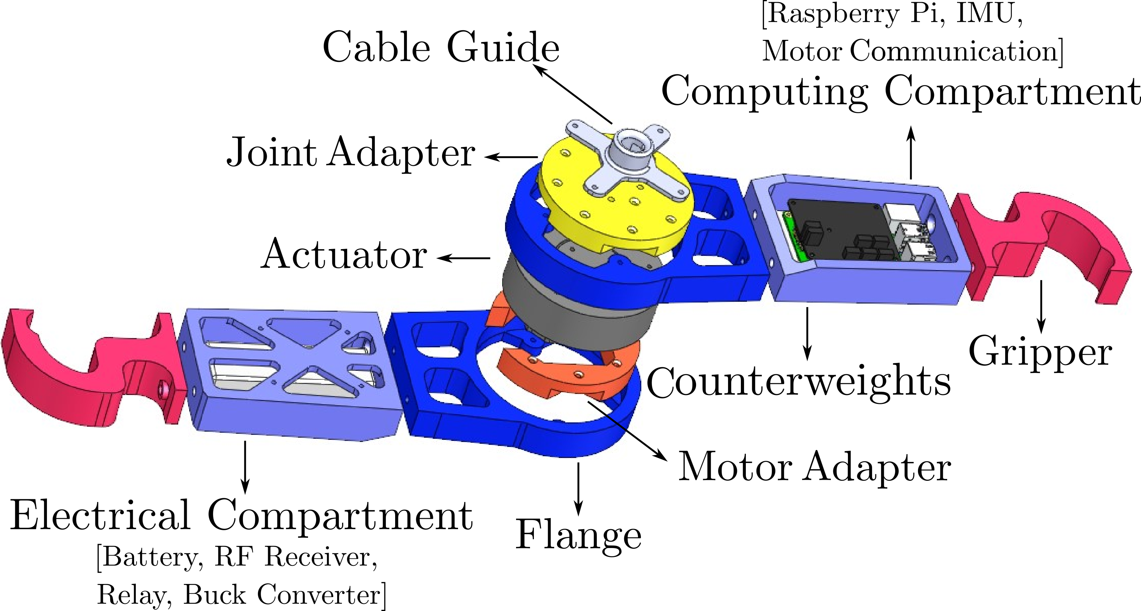
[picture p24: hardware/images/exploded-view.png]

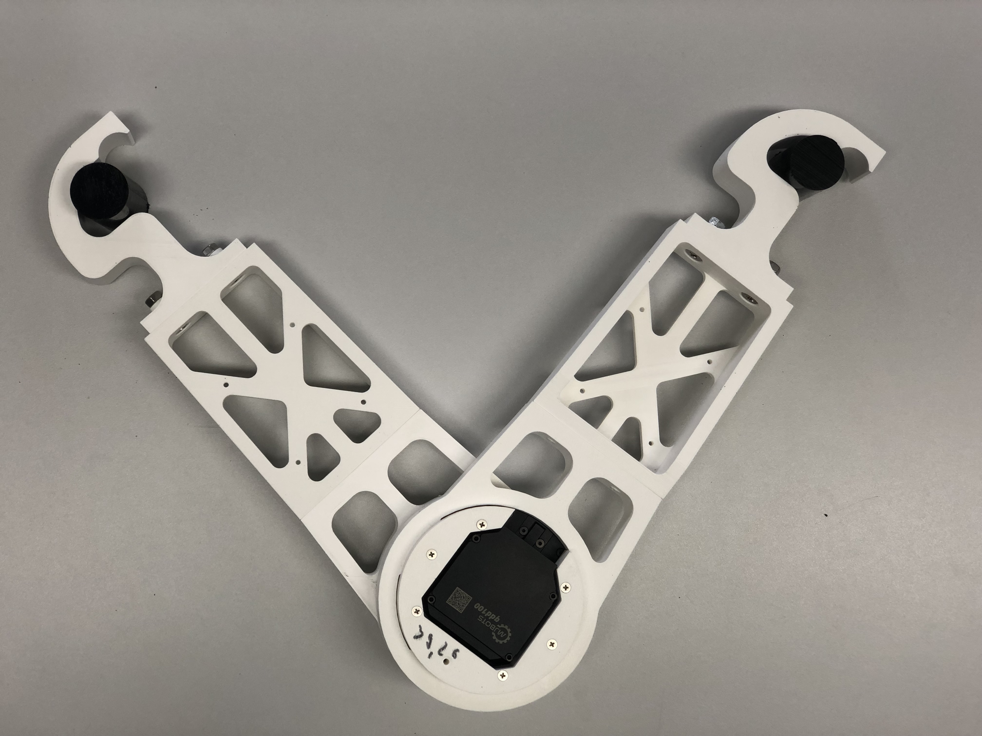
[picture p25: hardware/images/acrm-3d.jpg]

</div>

<div align="center">
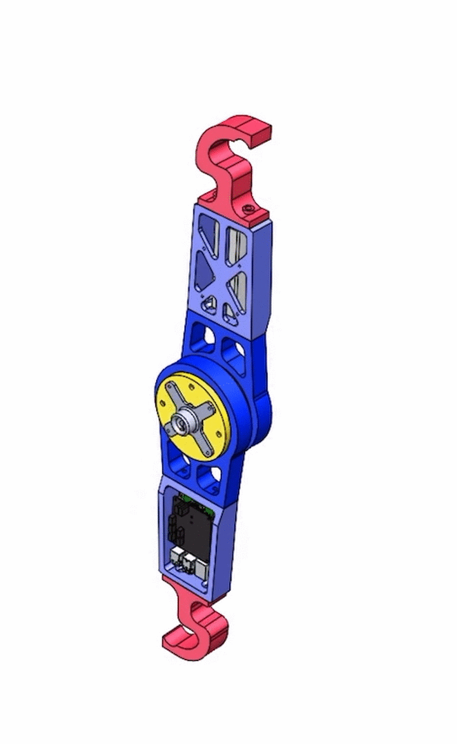
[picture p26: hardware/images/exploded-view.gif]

</div>

## Electronics
The schematic of the electrical diagram is shown in the following figure and components are described in individual subsections.

<div align="center">
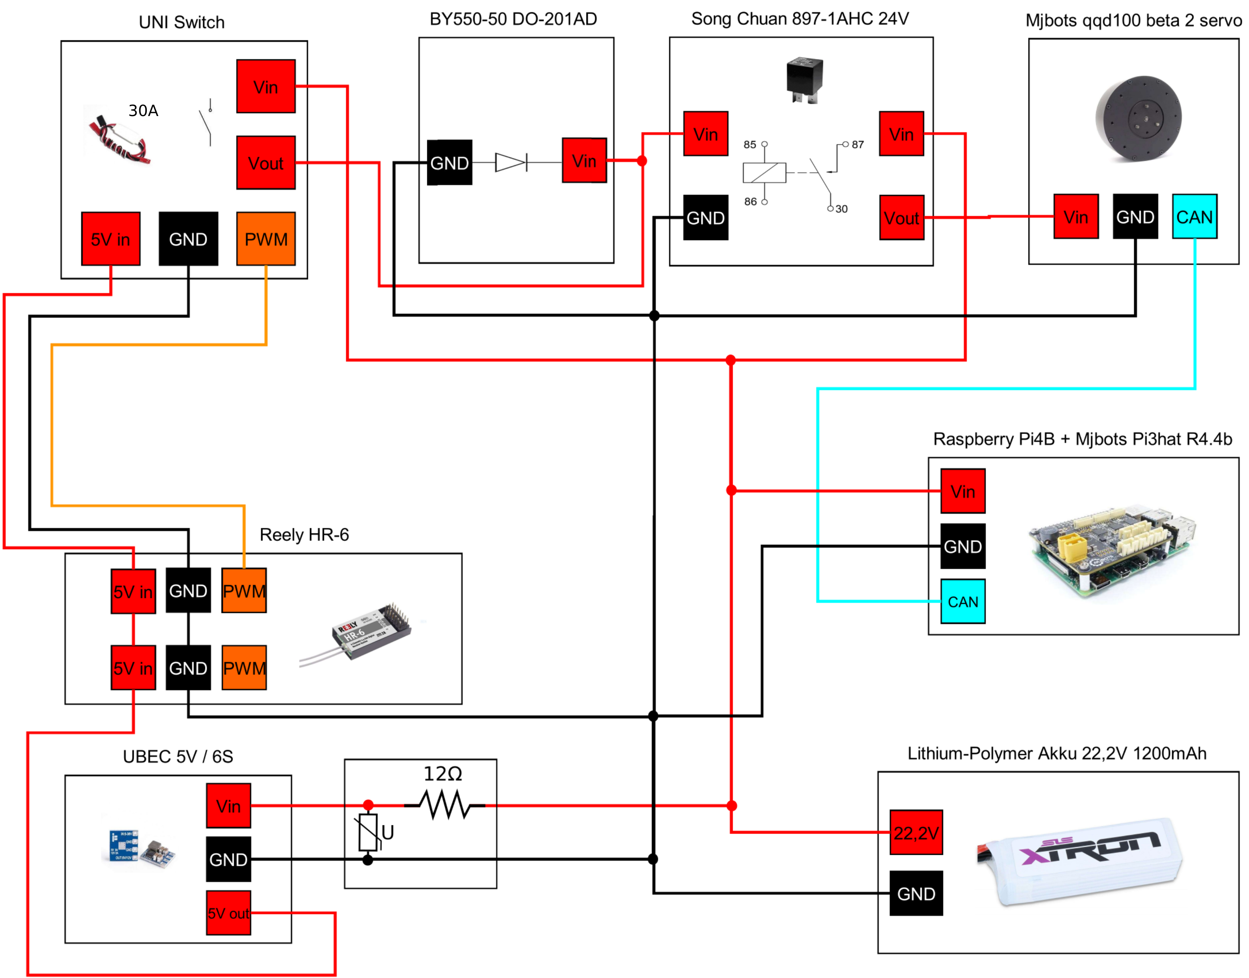
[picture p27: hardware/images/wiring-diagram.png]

</div>

### Battery
All electronics of the AcroMonk are powered by a LiPo battery with the following technical data:
- Capacity: $6\text{S}\ 1200 \text{ mAh}$ 
- Voltage: $22.2\text{V}$
- Continuous Discharge: max. $30\text{C } (36\text{A})$
- Burst Discharge:max. $60\text{C } (72\text{A})$
- Power: $26.64 \text{ WH}$

### Raspberry Pi 
A Raspberry Pi 4 Model B is used for the onboard computer, providing wireless communication capability. 
- [Setup guide](wireless-communication.md)
### pi3hat
[Mjbots pi3hat](https://mjbots.com/products/mjbots-pi3hat-r4-4b) is a daughterboard for the Raspberry Pi, and sits on top of it by connecting through the $40$ pin GPIO interface. The $\text{XT}30\text{-M}$ power connector on pi3hat enables the powering of the Raspberry Pi, and also provides CAN interfaces for communication with the actuator ([mjbots qdd 100 servo](https://mjbots.com/collections/servos-and-controllers/products/qdd100-beta-3)) and IMU sensor.

In order to read IMU data, one can use [pi3hat_tools](https://github.com/mjbots/pi3hat/) library provided by mjbots. 
- [IMU reading](https://github.com/mjbots/pi3hat/blob/master/lib/python/examples/imu_example.py)

### Actuator

A [qdd100 beta 3 servo](https://mjbots.com/collections/servos-and-controllers/products/qdd100-beta-3) is used as an actuator for the AcroMonk. 
Here are the useful links for documentation and also setting up the mjbots servo motor:
- [Documentation](https://github.com/mjbots/moteus)
- [Setup guide](https://www.youtube.com/watch?v=HHCBohdrCH8)

### Emergency Stop
To have the authority to disable the motor in case of the undesired behavior, a remote emergency stop is designed. A relay, diode, and a $30 \text{A}$ electronic switch are employed to disconnect the power. The triggering command is provided by a joystick that connects the electronic switch with an onboard receiver, which is powered by a buck converter.
A series combination of Varistor(voltage-dependant-resistor) and a resistor component is used to protect the buck conrverter from high-frequency voltage fluctuations.

# Mechatronics Integration
Here is the final integration of the AcroMonk.
<div align="center">
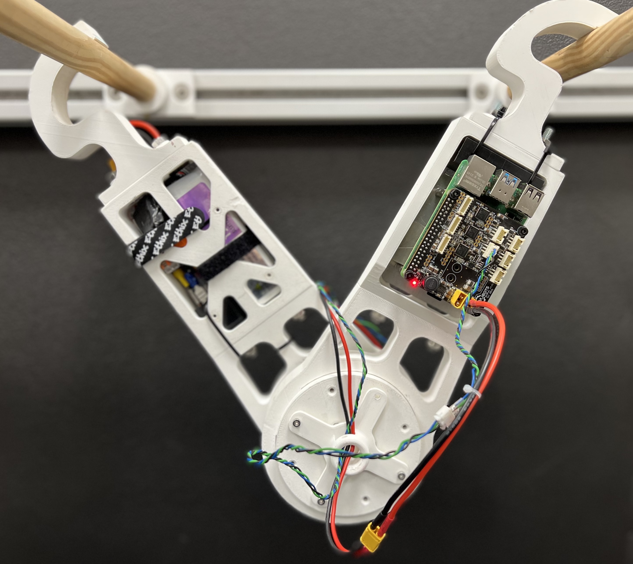
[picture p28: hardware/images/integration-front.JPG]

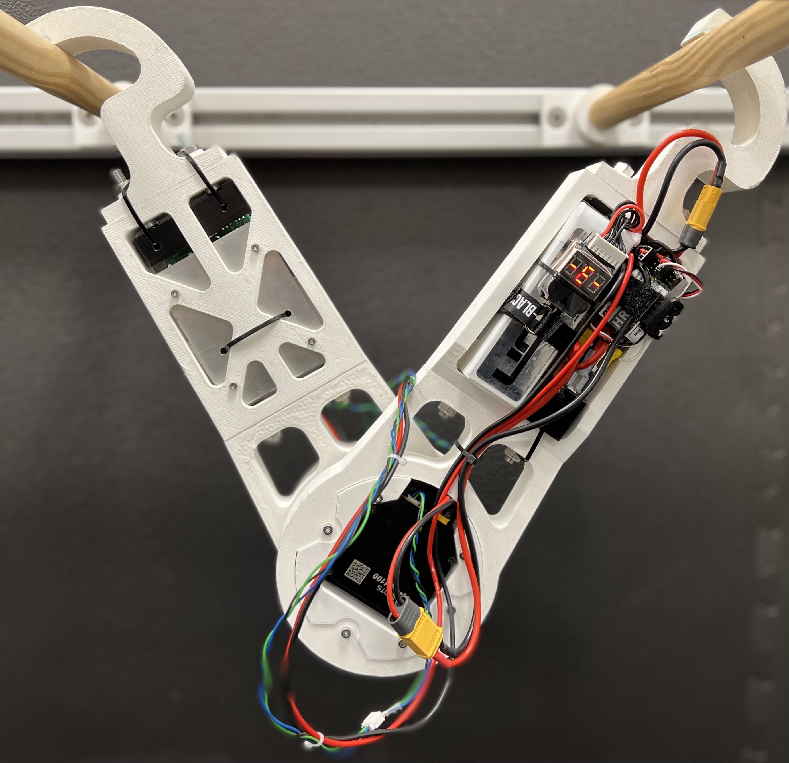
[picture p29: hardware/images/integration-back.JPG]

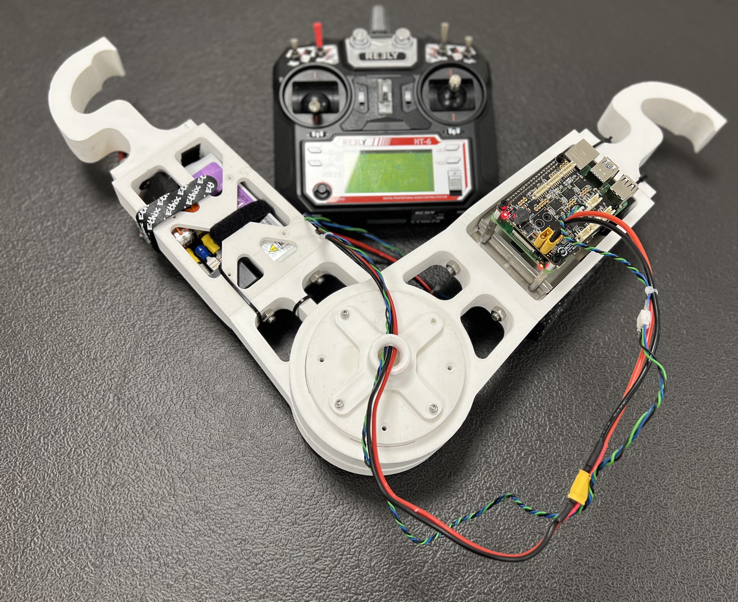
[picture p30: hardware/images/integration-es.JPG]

</div>

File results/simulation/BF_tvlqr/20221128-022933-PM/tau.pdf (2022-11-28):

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

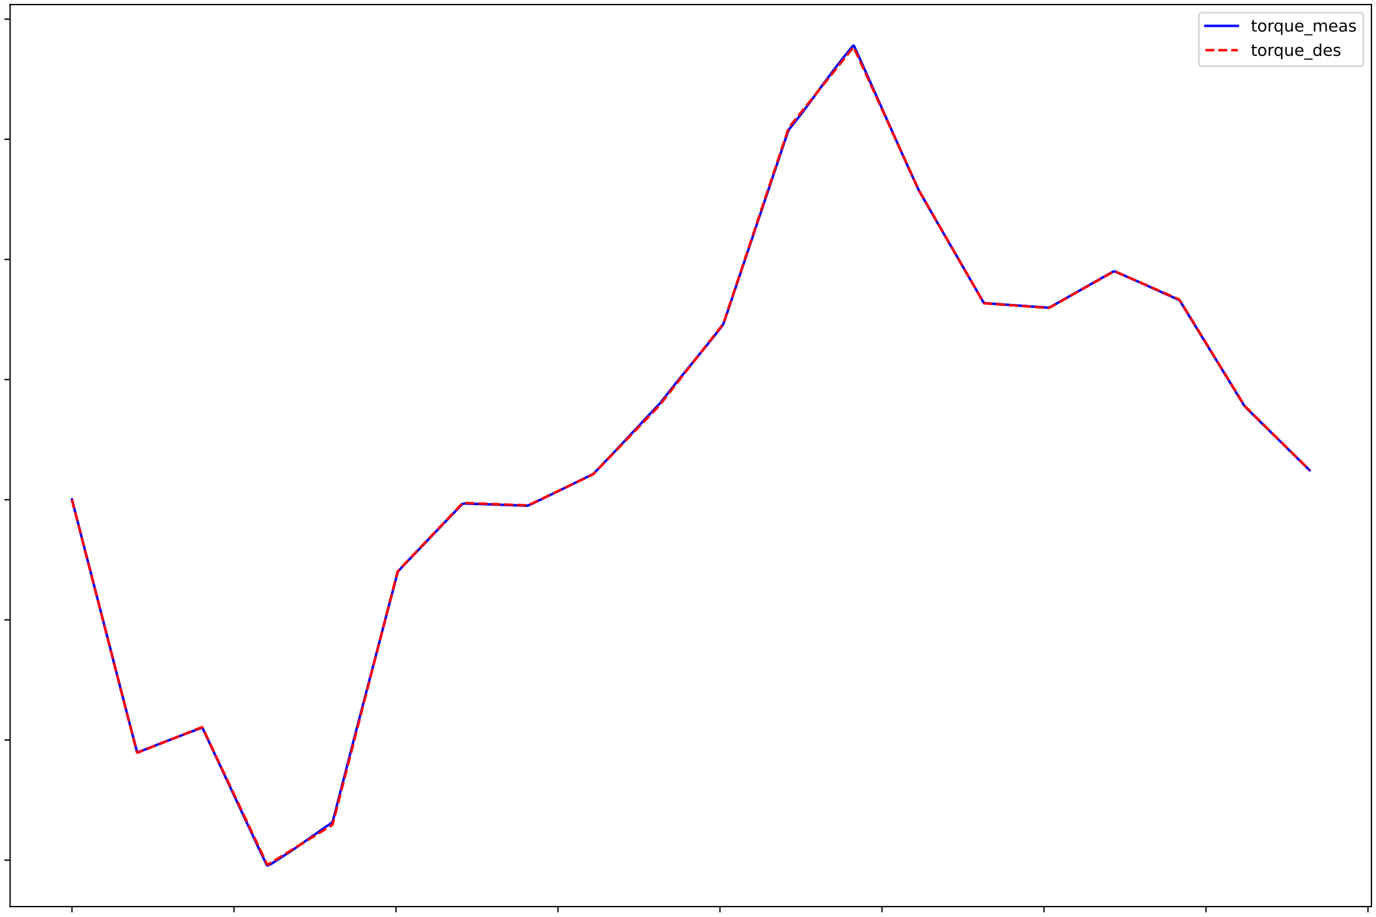
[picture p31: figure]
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

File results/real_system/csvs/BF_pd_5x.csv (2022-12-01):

meas_time | shoulder_des_pos_store | shoulder_meas_pos | shoulder_des_vel_store | shoulder_meas_vel | elbow_des_pos_store | elbow_meas_pos | elbow_des_vel_store | elbow_meas_vel | elbow_des_tau_store | elbow_meas_tau | elbow_cmd_tau | elbow_clipped_tau | raw_imu_pos | raw_imu_vel | k1_store | k2_store | k3_store | k4_store | state_machine_flag
6.318092346191406250e-03 | nan | -5.325990039598331727e-01 | nan | -7.763309828380625735e-03 | nan | -1.975431696499355905e+00 | nan | 6.303395087420910620e-03 | nan | 0.000000000000000000e+00 | 2.500000000000000000e+00 | 2.500000000000000000e+00 | nan | nan | nan | nan | nan | nan | 0.000000000000000000e+00
1.108503341674804688e-02 | nan | -5.326417983117819333e-01 | nan | -3.013909496526491830e-02 | nan | -1.975399676148436923e+00 | nan | 3.027470344006094258e-02 | nan | 0.000000000000000000e+00 | 2.500000000000000000e+00 | 2.500000000000000000e+00 | nan | nan | nan | nan | nan | nan | 0.000000000000000000e+00
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

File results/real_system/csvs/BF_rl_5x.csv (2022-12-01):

meas_time | shoulder_des_pos_store | shoulder_meas_pos | shoulder_des_vel_store | shoulder_meas_vel | elbow_des_pos_store | elbow_meas_pos | elbow_des_vel_store | elbow_meas_vel | elbow_des_tau_store | elbow_meas_tau | elbow_cmd_tau | elbow_clipped_tau | raw_imu_pos | raw_imu_vel | k1_store | k2_store | k3_store | k4_store
5.759477615356445312e-03 | nan | -5.133657823572259638e-01 | nan | -5.142561236634722588e-02 | nan | -1.988230848698276709e+00 | nan | 5.236681452230602940e-02 | nan | 0.000000000000000000e+00 | 2.500000000000000000e+00 | 2.500000000000000000e+00 | nan | nan | nan | nan | nan | nan
1.005339622497558594e-02 | nan | -5.132198044779787693e-01 | nan | 6.620233982556464336e-02 | nan | -1.988374659397140976e+00 | nan | -6.685897840767346390e-02 | nan | 0.000000000000000000e+00 | 2.500000000000000000e+00 | 2.500000000000000000e+00 | nan | nan | nan | nan | nan | nan
1.394748687744140625e-02 | nan | -5.132979279424692010e-01 | nan | -3.157536134288966428e-02 | nan | -1.988294702146600423e+00 | nan | 3.091879701200068650e-02 | nan | 0.000000000000000000e+00 | 2.500000000000000000e+00 | 2.500000000000000000e+00 | nan | nan | nan | nan | nan | nan
1.777029037475585938e-02 | nan | -5.146553928858250693e-01 | nan | -4.920771546485789849e-01 | nan | -1.986936552408498091e+00 | nan | 4.914205855713335569e-01 | nan | 1.908908605575561523e+00 | 2.500000000000000000e+00 | 2.500000000000000000e+00 | nan | nan | nan | nan | nan | nan
2.167701721191406250e-02 | nan | -5.183635680315017424e-01 | nan | -7.043660735246340954e-01 | nan | -1.983325368388188847e+00 | nan | 7.841231542196268611e-01 | nan | 2.758264303207397461e+00 | 2.500000000000000000e+00 | 2.500000000000000000e+00 | nan | nan | nan | nan | nan | nan
2.548503875732421875e-02 | nan | -5.182903434287342570e-01 | nan | -9.016652487247450720e-02 | nan | -1.982478420743705616e+00 | nan | 1.608686747688729546e-01 | nan | 2.791400432586669922e+00 | 2.500000000000000000e+00 | 2.500000000000000000e+00 | nan | nan | nan | nan | nan | nan
2.932333946228027344e-02 | nan | -5.180517149334171734e-01 | nan | 8.573101720326845032e-02 | nan | -1.982622231442569882e+00 | nan | 3.344213759355007393e-02 | nan | 2.385238885879516602e+00 | 2.500000000000000000e+00 | 2.500000000000000000e+00 | nan | nan | nan | nan | nan | nan
3.320002555847167969e-02 | nan | -5.188623216463765786e-01 | nan | -2.082299409632056841e-01 | nan | -1.981615556550519797e+00 | nan | 2.725246917244416034e-01 | nan | 2.386355638504028320e+00 | 2.500000000000000000e+00 | 2.500000000000000000e+00 | nan | nan | nan | nan | nan | nan
3.697824478149414062e-02 | nan | -5.196955893579842112e-01 | nan | -1.215792989954617848e-01 | nan | -1.980528924407929381e+00 | nan | 2.428760001888606579e-01 | nan | 2.604501485824584961e+00 | 2.500000000000000000e+00 | 2.500000000000000000e+00 | nan | nan | nan | nan | nan | nan
4.087018966674804688e-02 | nan | -5.200600456105894942e-01 | nan | -4.875035645475582491e-02 | nan | -1.980033638863012868e+00 | nan | 1.274352152053691012e-01 | nan | 2.473949432373046875e+00 | 2.500000000000000000e+00 | 2.500000000000000000e+00 | nan | nan | nan | nan | nan | nan
4.466390609741210938e-02 | nan | -5.207004416015079684e-01 | nan | -6.143245154057167673e-02 | nan | -1.979650143666041417e+00 | nan | 1.059871157716513190e-01 | nan | 2.454468488693237305e+00 | 2.500000000000000000e+00 | 2.500000000000000000e+00 | nan | nan | nan | nan | nan | nan
4.847311973571777344e-02 | nan | -5.213840661467279425e-01 | nan | -2.297326182944389450e-01 | nan | -1.978451721175505718e+00 | nan | 2.908186344491576758e-01 | nan | 2.493320703506469727e+00 | 2.500000000000000000e+00 | 2.500000000000000000e+00 | nan | nan | nan | nan | nan | nan
5.232548713684082031e-02 | nan | -5.217173802637926627e-01 | nan | -6.499104853232501311e-02 | nan | -1.977780604580805734e+00 | nan | 1.495139142546634548e-01 | nan | 2.586336851119995117e+00 | 2.500000000000000000e+00 | 2.500000000000000000e+00 | nan | nan | nan | nan | nan | nan
5.612516403198242188e-02 | nan | -5.223347014787114162e-01 | nan | -1.750922847357012646e-01 | nan | -1.977077467635186769e+00 | nan | 2.100729763941085182e-01 | nan | 2.460954666137695312e+00 | 2.500000000000000000e+00 | 2.500000000000000000e+00 | nan | nan | nan | nan | nan | nan
5.999088287353515625e-02 | nan | -5.227178203470446149e-01 | nan | -8.015726356104084516e-02 | nan | -1.976342497592162850e+00 | nan | 1.955641176876204701e-01 | nan | 2.507767677307128906e+00 | 2.500000000000000000e+00 | 2.500000000000000000e+00 | nan | nan | nan | nan | nan | nan
6.382656097412109375e-02 | nan | -5.231113148416106640e-01 | nan | -9.666291676038366032e-02 | nan | -1.975751338248003419e+00 | nan | 1.236501428904856897e-01 | nan | 2.554180383682250977e+00 | 2.500000000000000000e+00 | 2.500000000000000000e+00 | nan | nan | nan | nan | nan | nan
6.767845153808593750e-02 | nan | -5.238968916001836007e-01 | nan | -9.633273654000457098e-02 | nan | -1.975192012001248720e+00 | nan | 1.179727450783639997e-01 | nan | 2.515211820602416992e+00 | 2.500000000000000000e+00 | 2.500000000000000000e+00 | nan | nan | nan | nan | nan | nan
7.154107093811035156e-02 | nan | -5.243890937697268662e-01 | nan | -1.251225971150350946e-01 | nan | -1.974616769205791655e+00 | nan | 1.728545498458229634e-01 | nan | 2.485963106155395508e+00 | 2.500000000000000000e+00 | 2.500000000000000000e+00 | nan | nan | nan | nan | nan | nan
7.540607452392578125e-02 | nan | -5.250971462978477611e-01 | nan | -1.757338522057202979e-01 | nan | -1.973721884661686854e+00 | nan | 2.447685012362684764e-01 | nan | 2.382460594177246094e+00 | 2.500000000000000000e+00 | 2.500000000000000000e+00 | nan | nan | nan | nan | nan | nan
7.921528816223144531e-02 | nan | -5.261249821554017103e-01 | nan | -1.967426322687848561e-01 | nan | -1.972491629073746422e+00 | nan | 3.248830915419557153e-01 | nan | 2.513296365737915039e+00 | 2.500000000000000000e+00 | 2.500000000000000000e+00 | nan | nan | nan | nan | nan | nan
8.312344551086425781e-02 | nan | -5.268382505119686421e-01 | nan | -1.971259246077825544e-01 | nan | -1.971293206583210722e+00 | nan | 3.204673259847385935e-01 | nan | 2.501095294952392578e+00 | 2.500000000000000000e+00 | 2.500000000000000000e+00 | nan | nan | nan | nan | nan | nan
8.699011802673339844e-02 | nan | -5.278599064328082235e-01 | nan | -2.055153912670608929e-01 | nan | -1.970014826842134692e+00 | nan | 3.400229360743932117e-01 | nan | 2.510908603668212891e+00 | 2.500000000000000000e+00 | 2.500000000000000000e+00 | nan | nan | nan | nan | nan | nan
9.086608886718750000e-02 | nan | -5.291899159490025539e-01 | nan | -1.982014489759435505e-01 | nan | -1.968480846054249112e+00 | nan | 3.955354106774965905e-01 | nan | 2.466657400131225586e+00 | 2.500000000000000000e+00 | 2.500000000000000000e+00 | nan | nan | nan | nan | nan | nan
9.471249580383300781e-02 | nan | -5.305979313436530731e-01 | nan | -3.161251952712163527e-01 | nan | -1.966435475919230180e+00 | nan | 5.746895081361920177e-01 | nan | 2.444025993347167969e+00 | 2.500000000000000000e+00 | 2.500000000000000000e+00 | nan | nan | nan | nan | nan | nan
9.850287437438964844e-02 | nan | -5.320603051988967991e-01 | nan | -3.521161643712262257e-01 | nan | -1.964182441637023047e+00 | nan | 6.585891473500733451e-01 | nan | 2.295453548431396484e+00 | 2.500000000000000000e+00 | 2.500000000000000000e+00 | nan | nan | nan | nan | nan | nan
1.024122238159179688e-01 | nan | -5.340262646542601743e-01 | nan | -3.565500862372343316e-01 | nan | -1.961082646963846932e+00 | nan | 8.339584299674672740e-01 | nan | 2.505020856857299805e+00 | 2.500000000000000000e+00 | 2.500000000000000000e+00 | nan | nan | nan | nan | nan | nan
1.052272319793701172e-01 | nan | -5.361833078625242166e-01 | nan | -2.823521212911865863e-01 | nan | -1.957567149489266356e+00 | nan | 8.396359565163798999e-01 | nan | 2.590638399124145508e+00 | 2.500000000000000000e+00 | 2.500000000000000000e+00 | nan | nan | nan | nan | nan | nan
1.074931621551513672e-01 | nan | -5.365655382256351302e-01 | nan | -4.218997473554669808e-01 | nan | -1.955841421102894939e+00 | nan | 7.677221338627253644e-01 | nan | 2.424013853073120117e+00 | 2.500000000000000000e+00 | 2.500000000000000000e+00 | nan | nan | nan | nan | nan | nan
1.097619533538818359e-01 | nan | -5.374456973828731776e-01 | nan | -2.961029541056471315e-01 | nan | -1.953955965468956890e+00 | nan | 8.390052866807354848e-01 | nan | 2.316980838775634766e+00 | 2.500000000000000000e+00 | 2.500000000000000000e+00 | nan | nan | nan | nan | nan | nan
1.120183467864990234e-01 | nan | -5.387909729088162791e-01 | nan | -4.505490138308871906e-01 | nan | -1.951511183588264142e+00 | nan | 1.057901742288169800e+00 | nan | 2.303883314132690430e+00 | 2.500000000000000000e+00 | 2.500000000000000000e+00 | nan | nan | nan | nan | nan | nan
1.142592430114746094e-01 | nan | -5.405809728739758846e-01 | nan | -6.925370838630992010e-01 | nan | -1.948363264761952429e+00 | nan | 1.343034353560210503e+00 | nan | 2.186639070510864258e+00 | 2.500000000000000000e+00 | 2.500000000000000000e+00 | nan | nan | nan | nan | nan | nan
1.189095973968505859e-01 | nan | -5.410106728021055744e-01 | nan | 4.433472166290948202e-01 | 0.000000000000000000e+00 | -1.942275278510031233e+00 | 0.000000000000000000e+00 | 1.050332487112595192e+00 | nan | 0.000000000000000000e+00 | 1.634011691171307623e+00 | 1.634011691171307623e+00 | -2.483285951312137030e+00 | 1.493679703741690012e+00 | nan | nan | nan | nan
1.312406063079833984e-01 | nan | -5.365845513941200906e-01 | nan | -1.420343030059309397e+00 | 0.000000000000000000e+00 | -1.928405597970736629e+00 | 0.000000000000000000e+00 | 2.357400028316418261e+00 | nan | 6.795340776443481445e-01 | 1.577821056966370206e+00 | 1.577821056966370206e+00 | -2.464990149364856720e+00 | 9.370569982571088641e-01 | nan | nan | nan | nan
1.437518596649169922e-01 | nan | -5.447492606228498957e-01 | nan | 6.825052161110960469e-01 | 0.000000000000000000e+00 | -1.894274525440281076e+00 | 0.000000000000000000e+00 | 2.587019837291705482e+00 | nan | 1.340139865875244141e+00 | 1.138790868098750186e+00 | 1.138790868098750186e+00 | -2.439023786063131194e+00 | 3.269525053402801529e+00 | nan | nan | nan | nan
1.563217639923095703e-01 | nan | -5.441620951406354045e-01 | nan | 3.810863427982984497e-01 | 0.000000000000000000e+00 | -1.855269805697142615e+00 | 0.000000000000000000e+00 | 3.226674283798343978e+00 | nan | 9.797718524932861328e-01 | 9.112255117529061144e-01 | 9.112255117529061144e-01 | -2.399431900837778020e+00 | 3.607760626596642428e+00 | nan | nan | nan | nan
1.689040660858154297e-01 | nan | -5.385523950230970414e-01 | nan | 2.520478406384181191e-01 | 0.000000000000000000e+00 | -1.808515412017549506e+00 | 0.000000000000000000e+00 | 3.935717579760510620e+00 | nan | 1.014868378639221191e+00 | 2.570496981204233311e-01 | 2.570496981204233311e-01 | -2.347067807040646326e+00 | 4.187765420398928740e+00 | nan | nan | nan | nan
1.815218925476074219e-01 | nan | -5.258881491744960002e-01 | nan | 1.106851485764639875e+00 | 0.000000000000000000e+00 | -1.757127055623380452e+00 | 0.000000000000000000e+00 | 4.200032281597348316e+00 | nan | 9.767620265483856201e-02 | -2.980188307640266321e-01 | -2.980188307640266321e-01 | -2.283015204797876674e+00 | 5.306883767361988191e+00 | nan | nan | nan | nan
1.940653324127197266e-01 | nan | -5.128397793345178535e-01 | nan | 9.941128111223189734e-01 | 0.000000000000000000e+00 | -1.703389791147761567e+00 | 0.000000000000000000e+00 | 4.702167185554476880e+00 | nan | -7.492208480834960938e-02 | -3.709357186117426264e-01 | -3.709357186117426264e-01 | -2.216229570482279421e+00 | 5.696279996676795854e+00 | nan | nan | nan | nan
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

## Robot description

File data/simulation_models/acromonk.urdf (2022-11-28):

<?xml version="1.0" encoding="utf-8"?>
<!-- This URDF was automatically created by SolidWorks to URDF Exporter! Originally created by Stephen Brawner (brawner@gmail.com) 
     Commit Version: 1.6.0-4-g7f85cfe  Build Version: 1.6.7995.38578
     For more information, please see http://wiki.ros.org/sw_urdf_exporter -->
<robot name="acromonk">
  <joint name="base_weld" type="fixed">
      <origin xyz="0 0 0" rpy="0 0 0" /> 
      <parent link="world"/>
      <child link="Base"/>
  </joint>    
  <link name="Base">
    <inertial>
      <origin xyz="0.0536 0.69428 -0.16917" rpy="0 0 0" />
      <mass value="5.9209" />
      <inertia ixx="0.86611" ixy="3.0201E-12" ixz="-8.3865E-08" iyy="0.13388" iyz="2.0135E-12" izz="0.76254" />
    </inertial>
    <visual>
      <origin xyz="0 0 0" rpy="0 0 0" />
      <geometry>
        <mesh filename="meshes/Base.obj" />
      </geometry>
      <material name="">
        <color rgba="0.79216 0.81961 0.93333 1" />
      </material>
    </visual>
  </link>
  <link name="stick_2">
    <inertial>
      <origin xyz="0.0536 0 0" rpy="0 0 0" />
      <mass value="0.062168" />
      <inertia ixx="4.4463E-06" ixy="-1.0251E-21" ixz="1.5345E-20" iyy="0.00084889" iyz="-2.4293E-22" izz="0.00084889" />
    </inertial>
    <visual>
      <origin xyz="0 0 0" rpy="0 0 0" />
      <geometry>
        <mesh filename="meshes/stick_2.obj" />
      </geometry>
      <material name="">
        <color rgba="1 1 1 1" />
      </material>
    </visual>
  </link>
  <joint name="stick_2" type="fixed">
    <origin xyz="0 0.34 0" rpy="0 0 0" />
    <parent link="Base" />
    <child link="stick_2" />
    <axis xyz="0 0 0" />
  </joint>
  <link name="hook_1">
    <inertial>
      <origin xyz="-0.0074828 0.23347 -0.020697" rpy="0 0 0" />
      <mass value="1.0419" />
      <inertia ixx="0.0017085" ixy="-1.1165E-05" ixz="-5.9438E-12" iyy="0.00071761" iyz="-4.3578E-06" izz="0.0011807" />
    </inertial>
    <visual>
      <origin xyz="0 0 0" rpy="0 0 0" />
      <geometry>
        <mesh filename="meshes/hook_1.obj" />
      </geometry>
      <material name="">
        <color rgba="0.75294 0.75294 0.75294 1" />
      </material>
    </visual>
  </link>
  <joint name="virtul_joint_hook_1" type="revolute">
    <origin xyz="0 0 0" rpy="-1.5708 0 0" />
    <parent link="Base" />
    <child link="hook_1" />
    <axis xyz="1 0 0" />
    <limit lower="-3.1415926" upper="3.1415926" effort="16" velocity="43" />
  </joint>
  <link name="link_2">
    <inertial>
      <origin xyz="0.00039594 0.091773 3.1856E-05" rpy="0 0 0" />
      <mass value="0.49759" />
      <inertia ixx="0.00099182" ixy="-2.7785E-06" ixz="-1.7253E-10" iyy="0.0003858" iyz="-2.3071E-08" izz="0.00063822" />
    </inertial>
    <visual>
      <origin xyz="0 0 0" rpy="0 0 0" />
      <geometry>
        <mesh filename="meshes/link_2.obj" />
      </geometry>
      <material name="">
        <color rgba="0 0.75294 0 1" />
      </material>
    </visual>
  </link>
  <joint name="joint_1" type="revolute">
    <origin xyz="0.0221 0.31401 -0.02" rpy="0 0 0" />
    <parent link="hook_1" />
    <child link="link_2" />
    <axis xyz="1 0 0" />
    <limit lower="-3.1415926" upper="3.1415926" effort="16" velocity="43" />
  </joint>
  <transmission type="SimpleTransmission" name="elbow_trans">
    <actuator name="joint_1"/>
    <joint name="joint_1"/>
    <mechanicalReduction>1</mechanicalReduction>
  </transmission>    
  <link name="hook_2">
    <inertial>
      <origin xyz="0.0236 -0.035143 0.027199" rpy="0 0 0" />
      <mass value="0.1009" />
      <inertia ixx="0.00014182" ixy="-1.0624E-11" ixz="5.6845E-12" iyy="3.885E-05" iyz="-4.3578E-06" izz="0.00011814" />
    </inertial>
    <visual>
      <origin xyz="0 0 0" rpy="0 0 0" />
      <geometry>
        <mesh filename="meshes/hook_2.obj" />
      </geometry>
      <material name="">
        <color rgba="0.75294 0.75294 0.75294 1" />
      </material>
    </visual>
  </link>
  <joint name="virtual_joint_hook_2" type="fixed">
    <origin xyz="-0.0221 0.31401 -0.02" rpy="0 0 0" />
    <parent link="link_2" />
    <child link="hook_2" />
    <axis xyz="0 0 0" />
  </joint>
  <link name="IMU">
    <inertial>
      <origin xyz="0.0071635 -0.0014434 0.00087298" rpy="0 0 0" />
      <mass value="0.032575" />
      <inertia ixx="1.2236E-05" ixy="-3.9023E-07" ixz="-5.1339E-07" iyy="8.4139E-06" iyz="3.5873E-07" izz="2.0142E-05" />
    </inertial>
    <visual>
      <origin xyz="0 0 0" rpy="0 0 0" />
      <geometry>
        <mesh filename="meshes/IMU.obj" />
      </geometry>
      <material name="">
        <color rgba="0.2 0.2 0.2 1" />
      </material>
    </visual>
  </link>
  <joint name="IMU" type="fixed">
    <origin xyz="0.00959 0.15306 0.0015645" rpy="0 1.5708 0" />
    <parent link="link_2" />
    <child link="IMU" />
    <axis xyz="0 0 0" />
  </joint>
  <link name="stick_1">
    <inertial>
      <origin xyz="0 0 0" rpy="0 0 0" />
      <mass value="0" />
      <inertia ixx="0" ixy="0" ixz="0" iyy="0" iyz="0" izz="0" />
    </inertial>
    <visual>
      <origin xyz="0 0 0" rpy="0 0 0" />
      <geometry>
        <mesh filename="meshes/stick_1.obj" />
      </geometry>
      <material name="">
        <color rgba="1 1 1 1" />
      </material>
    </visual>
  </link>
  <joint name="stick_1" type="fixed">
    <origin xyz="0 -0.34 0" rpy="0 0 0" />
    <parent link="Base" />
    <child link="stick_1" />
    <axis xyz="0 0 0" />
  </joint>
</robot>

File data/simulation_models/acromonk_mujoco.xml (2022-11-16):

<mujoco model="20220510_ShwingBotV1">
<!--    <size nuserdata="100" nuser_actuator="1"/>-->
    <compiler angle="radian" meshdir="meshes/"/>
    <size njmax="500" nconmax="100" />
    <contact>
        <exclude body1="hook_1" body2="link_2" />
        <exclude body1="base_stick" body2="hook_1" />
    </contact>
    <asset>
        <texture name="texplane" type="2d" builtin="checker" rgb1=".867 .541 .236" rgb2=".953 .694 .392" width="100" height="100"/>
        <texture type="skybox" builtin="gradient" width="128" height="128" rgb1="0.0 0.699 0.839" rgb2="0.0 0.699 0.839"/>
        <material name='MatPlane' reflectance='0.0' texture="texplane" texrepeat="5 5" texuniform="true"/>
        <material name='black_metal' reflectance='0.2' shininess='0.5' rgba="0.15 0.15 0.15 1"/>
        <material name='black_rough_metal' reflectance='0.1' shininess='0.3' rgba="0.0 0.0 0.0 1"/>
        <material name='wood' reflectance='0.1' shininess='0.3' rgba="0.58 0.43 0.2 1"/>
        <mesh name="stick_2" file="stick_2.STL" />
        <mesh name="hook_1" file="hook_1.STL" />
        <mesh name="link_2" file="link_2.STL" />
        <mesh name="hook_2_lower" file="hook_2_lower.STL" />
        <mesh name="hook_2_upper_lower" file="hook_2_upper.STL" />
        <mesh name="hook_2_upper_tip" file="hook_2_upper_tip.STL" />
        <mesh name="IMU" file="IMU.STL" />
        <mesh name="stick_1" file="stick_1.STL" />
    </asset>
    <worldbody>
        <light directional='false' diffuse='1.0 1.0 1.0' specular='0.3 0.3 0.3' pos='1.5 -1.0 4.0' dir='0 -.15 -1'/>
        <geom name='floor' pos='0 0 -0.75' size='10 10 10' type='plane' material="MatPlane" condim='3'/>
        <geom name='stick_target' pos="0 0.34 0" type="mesh" rgba="1 1 1 1" mesh="stick_2" />
        <geom name='stick_start' pos="0 -0.34 0" type="mesh" rgba="1 1 1 1" mesh="stick_1" />
        <body name="base_stick" pos="0 0 0">
            <geom name='stick_base' type="mesh" rgba="0.79216 0.81961 0.93333 1" mesh="stick_2" />
            <body name="hook_1" pos="0 0 0" quat="0.707105 -0.707108 0 0">
            <inertial pos="-0.0074828 0.23347 -0.020697" quat="0.703762 0.710413 -0.00403474 -0.00393152" mass="1.0419" diaginertia="0.00170863 0.00118074 0.000717443" />
            <joint name="virtual_joint_hook_1" pos="0 0 0" axis="1 0 0" damping="0.044" />
            <geom name='hook_1' type="mesh" rgba="0.75294 0.75294 0.75294 1" mesh="hook_1" />
                <body name="link_2" pos="0.0221 0.31401 -0.02">
                    <inertial pos="0.00109212 0.124776 0.00088714" quat="0.695157 0.718837 -0.00537166 -0.000151466" mass="0.631065" diaginertia="0.00412099 0.00373661 0.000438013" />
                    <joint name="joint_1" pos="0 0 0" axis="1 0 0" damping="0.06"/>
                    <geom name='link_2' type="mesh" rgba="0 0.75294 0 1" mesh="link_2" />
<!--                    <geom pos="-0.0221 0.31401 -0.02" type="mesh" rgba="0.75294 0.75294 0.75294 1" mesh="hook_2" />-->
                    <geom pos="0.00959 0.15306 0.0015645" quat="0.707105 0 0.707108 0" type="mesh" rgba="0.2 0.2 0.2 1" mesh="IMU" />
                    <body name="hook_2" pos="-0.0221 0.31401 -0.02">
                        <geom name='hook_2_lower' type="mesh" rgba="0.75294 0.75294 0.75294 1" mesh="hook_2_lower" />
                        <geom name='hook_2_upper' type="mesh" rgba="0.75294 0.75294 0.75294 1" mesh="hook_2_upper_lower" />
                        <body name="hook_2_tip">
                            <geom name='hook_2_tip' type="mesh" rgba="0.75294 0.75294 0.75294 1" mesh="hook_2_upper_tip" />
                        </body>
                    </body>
                </body>
            </body>
        </body>
    </worldbody>

    <actuator>
        <motor joint="joint_1" name="elbow_motor" gear="1" forcelimited="true" forcerange="-5 5"/>
    </actuator>
</mujoco>

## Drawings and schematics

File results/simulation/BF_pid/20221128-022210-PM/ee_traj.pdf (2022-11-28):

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

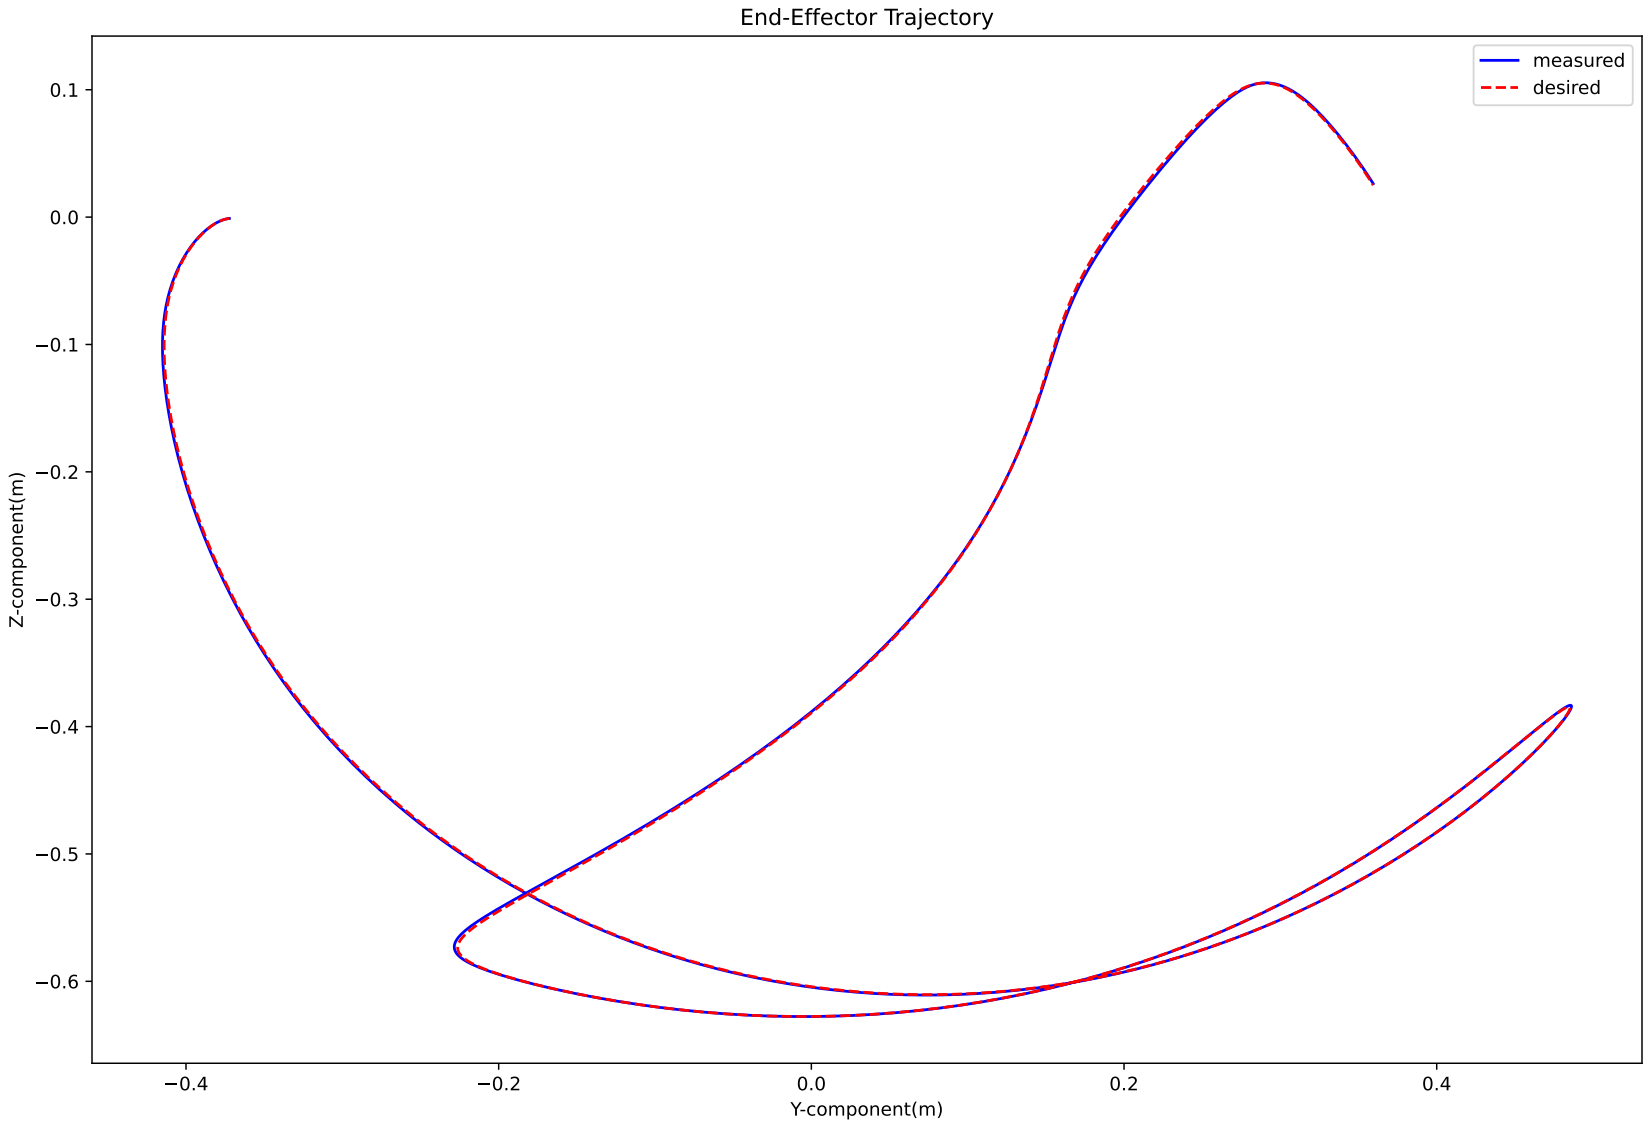
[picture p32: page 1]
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

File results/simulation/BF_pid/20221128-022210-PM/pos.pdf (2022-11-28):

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

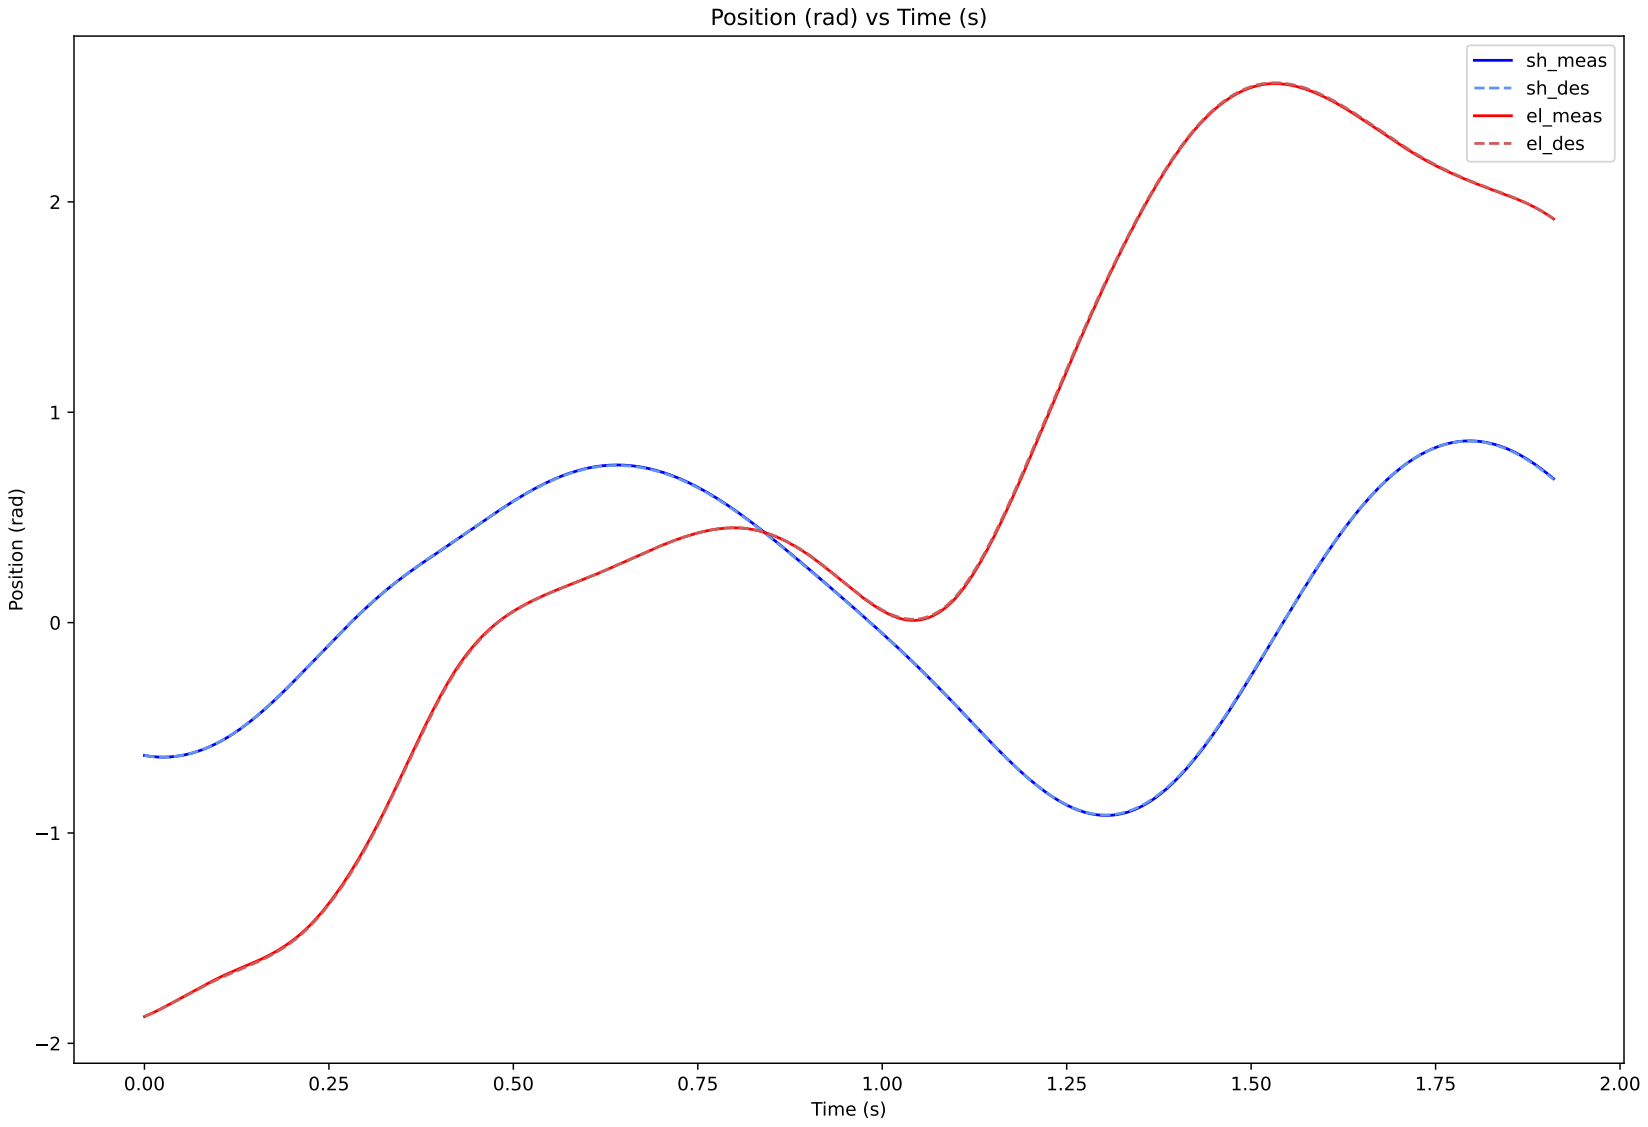
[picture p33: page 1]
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

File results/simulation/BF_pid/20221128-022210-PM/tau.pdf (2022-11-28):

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

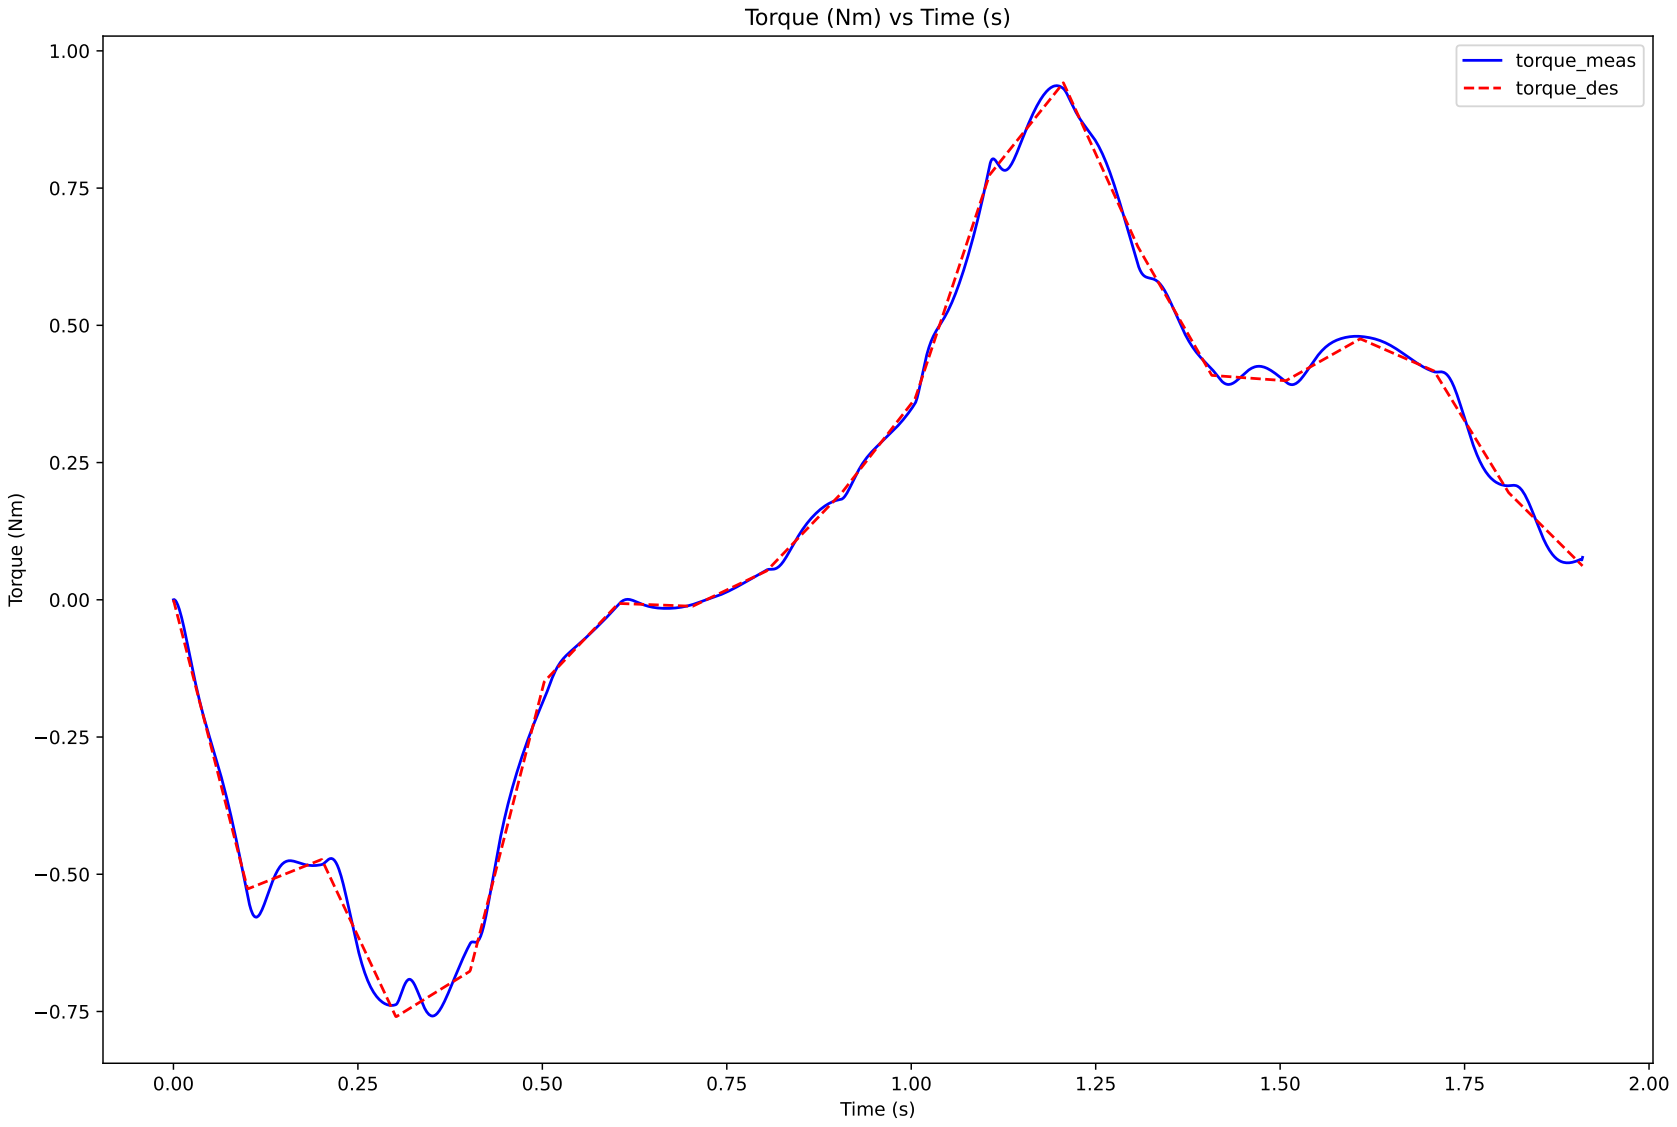
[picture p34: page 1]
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

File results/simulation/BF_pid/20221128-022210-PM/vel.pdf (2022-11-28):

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

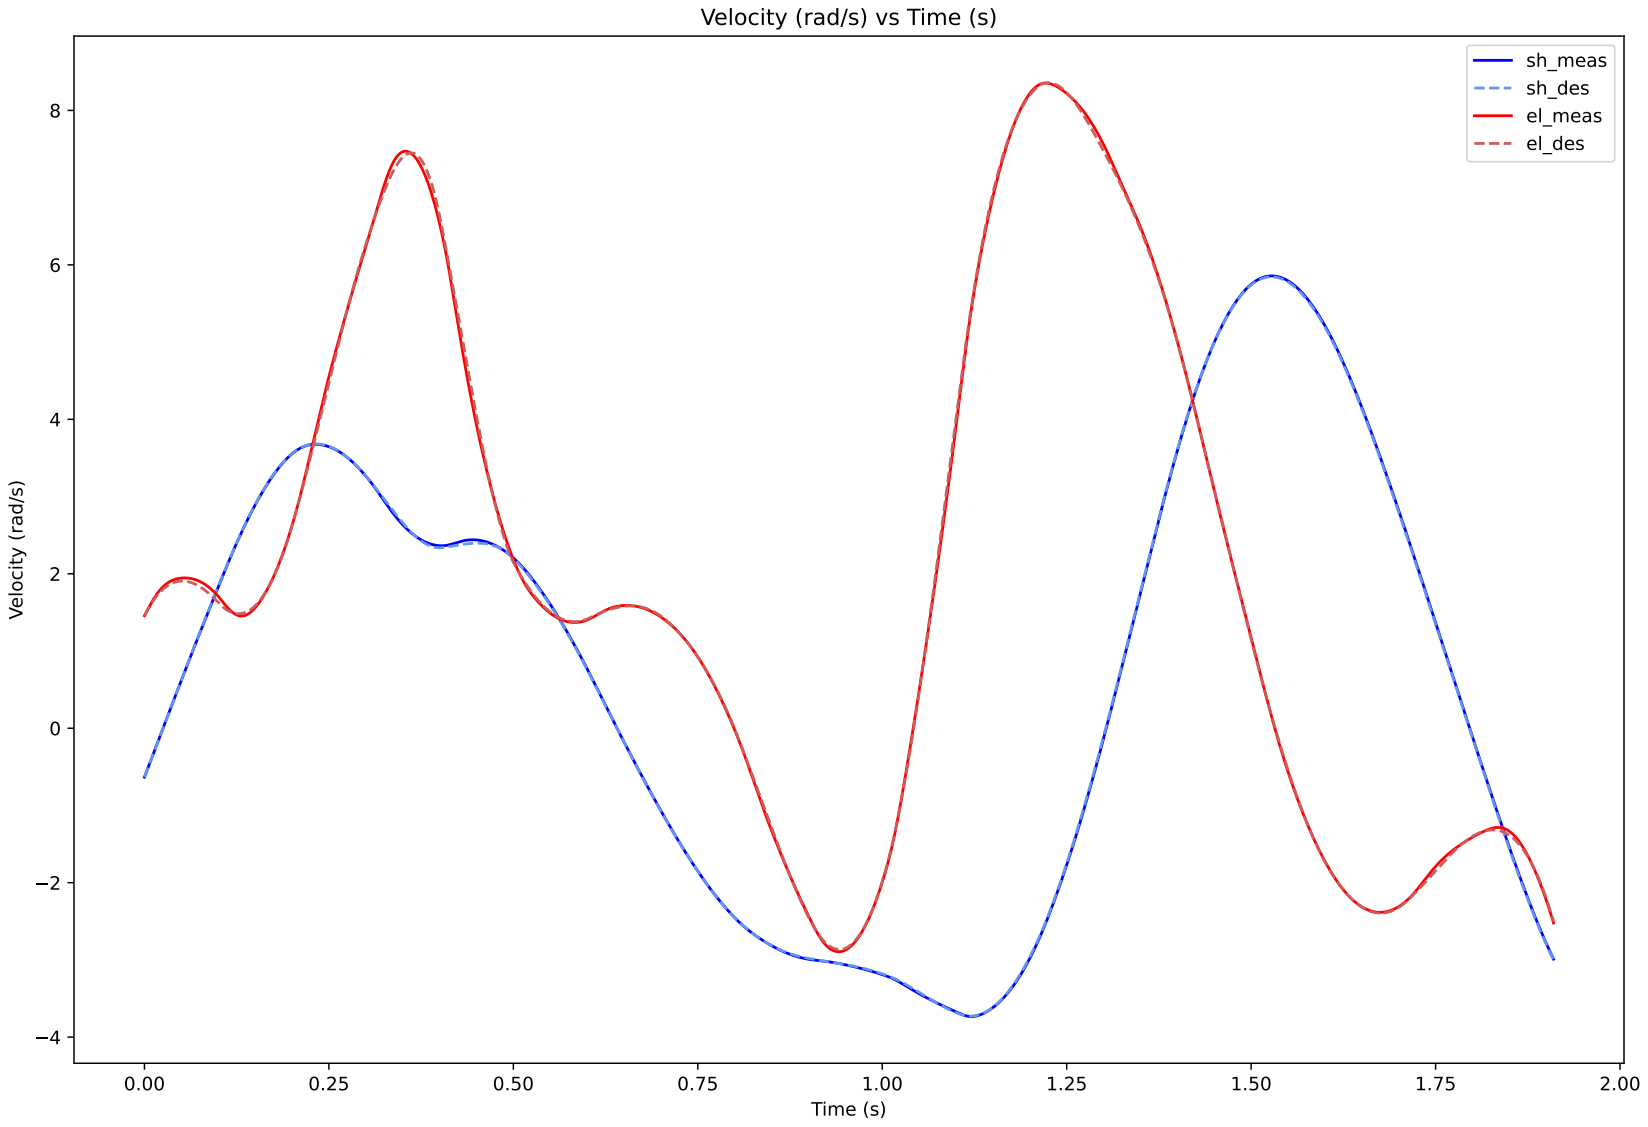
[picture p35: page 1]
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

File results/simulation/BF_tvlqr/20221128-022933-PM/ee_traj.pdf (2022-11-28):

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

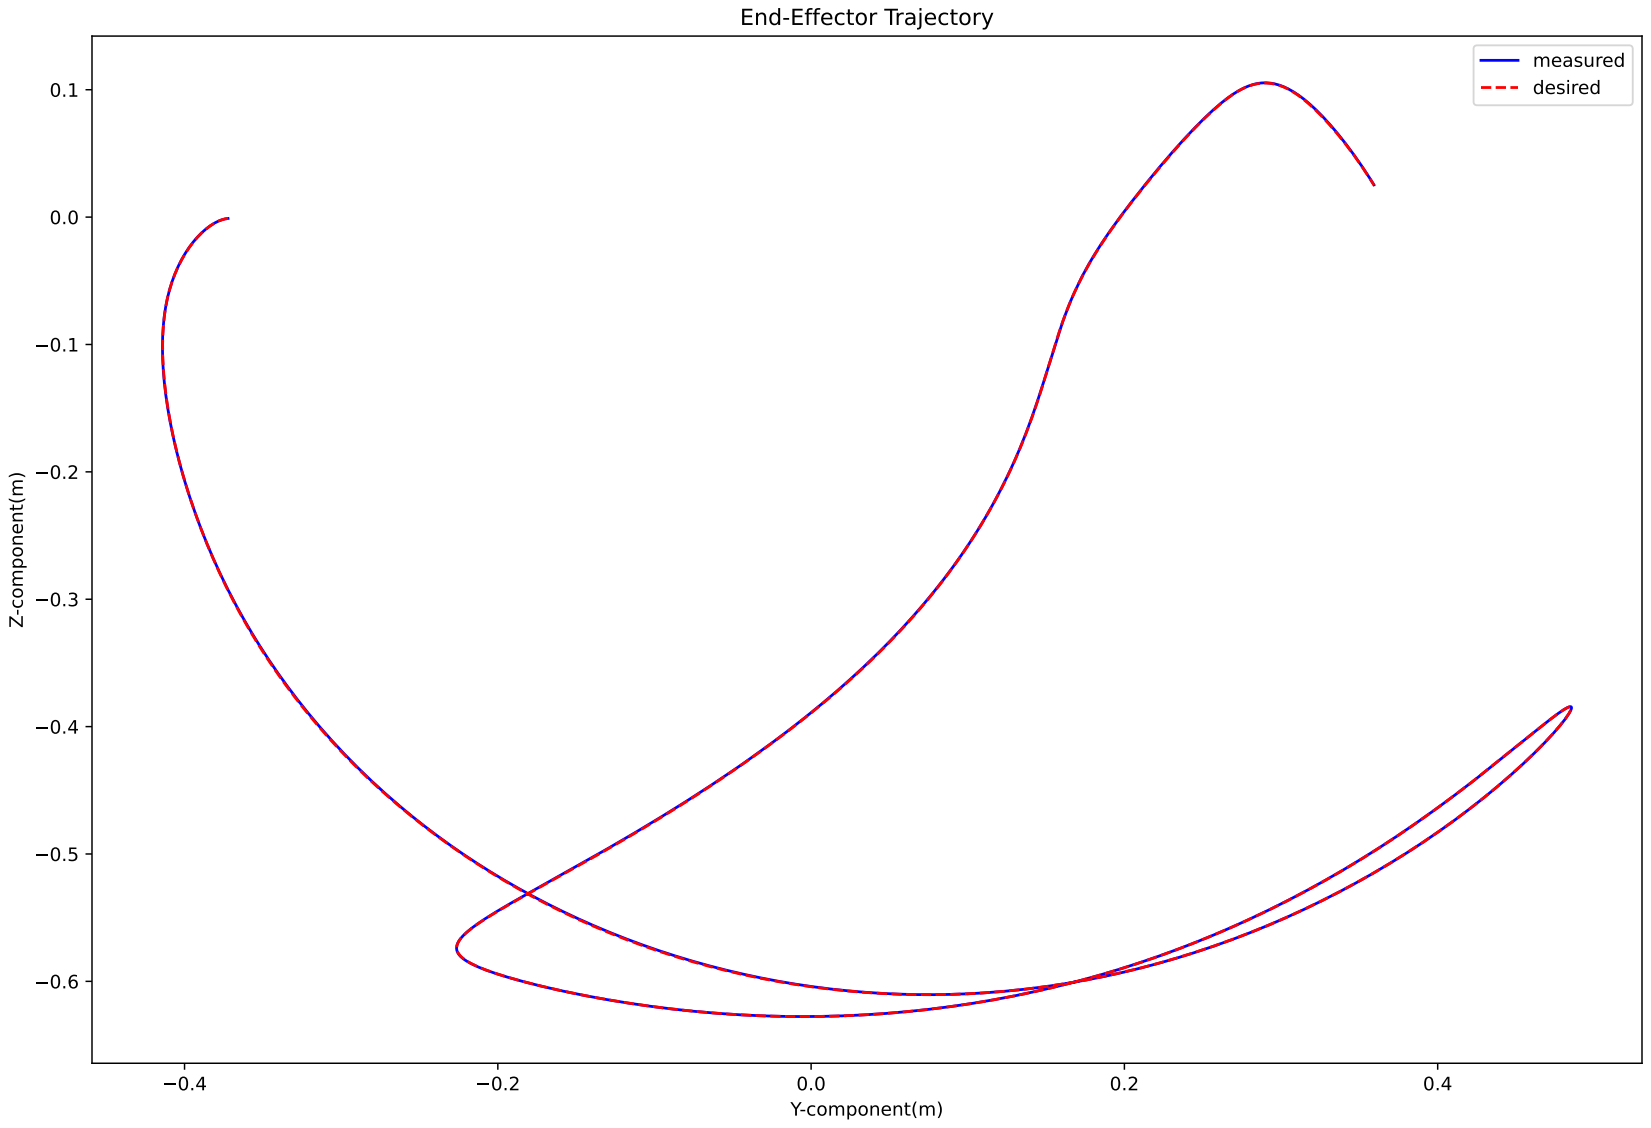
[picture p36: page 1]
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

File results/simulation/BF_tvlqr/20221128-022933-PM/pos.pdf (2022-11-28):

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

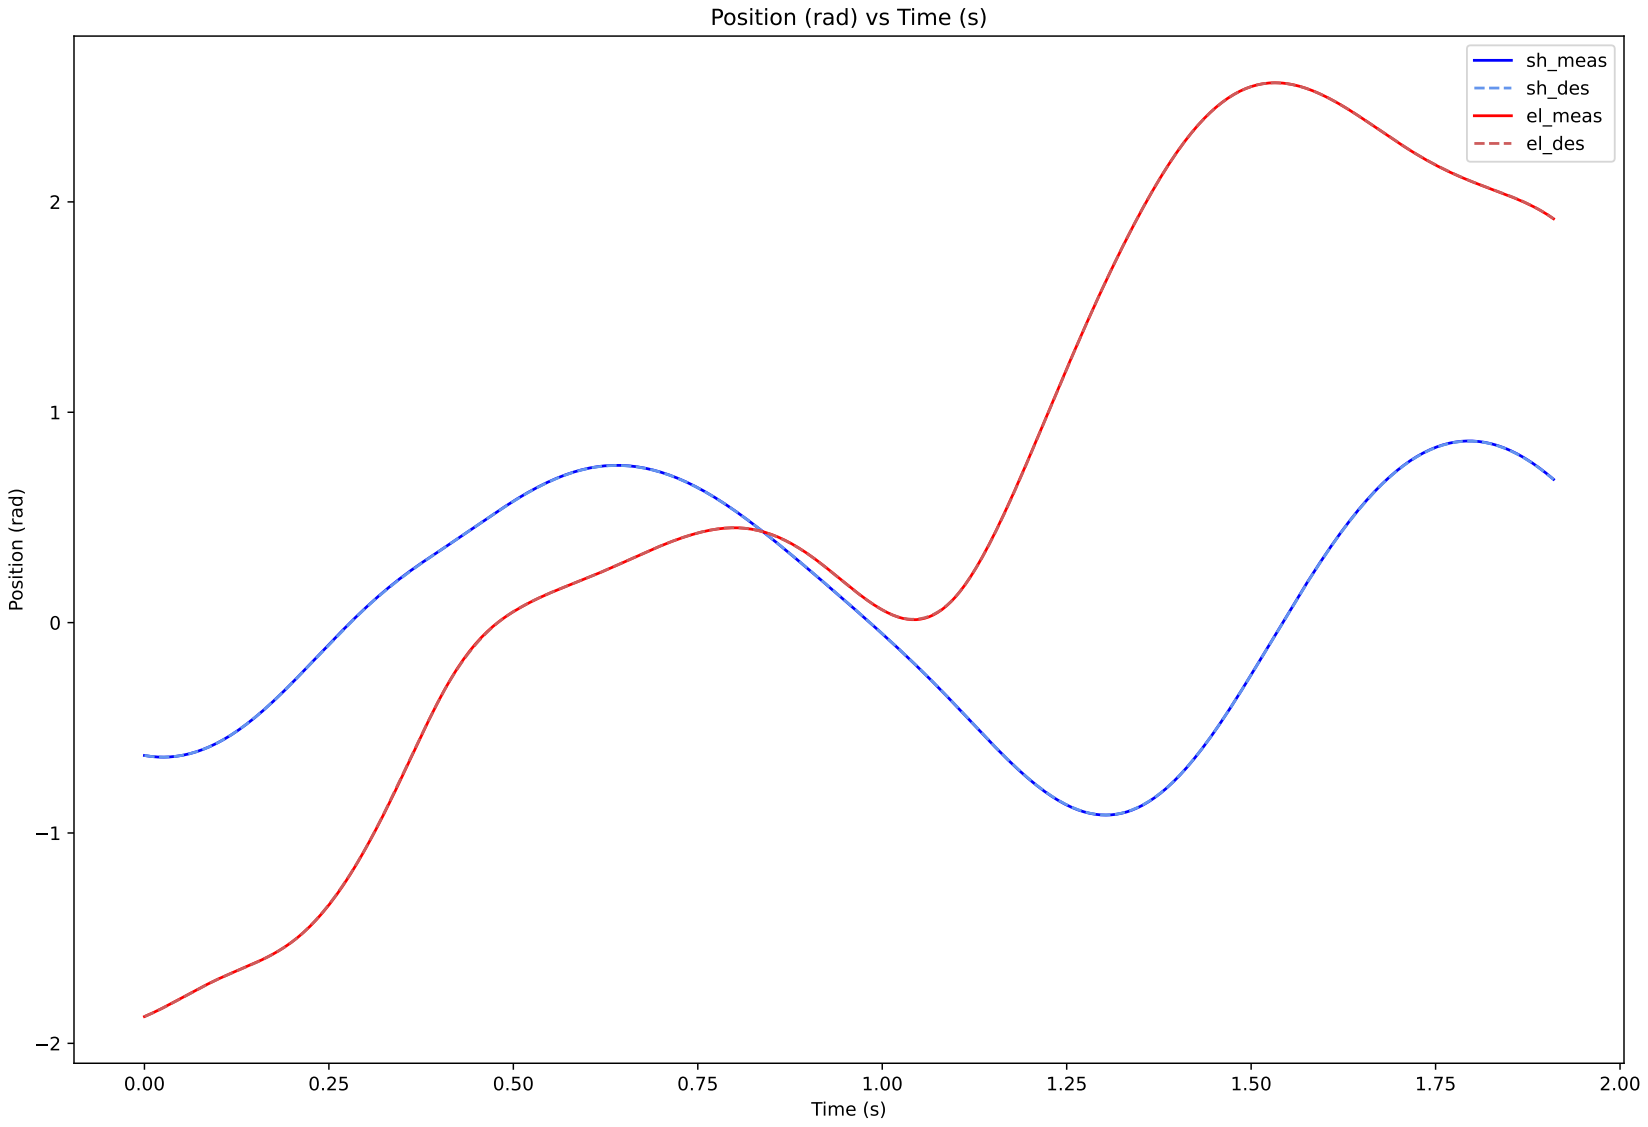
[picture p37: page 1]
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

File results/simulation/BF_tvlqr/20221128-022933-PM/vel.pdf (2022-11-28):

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

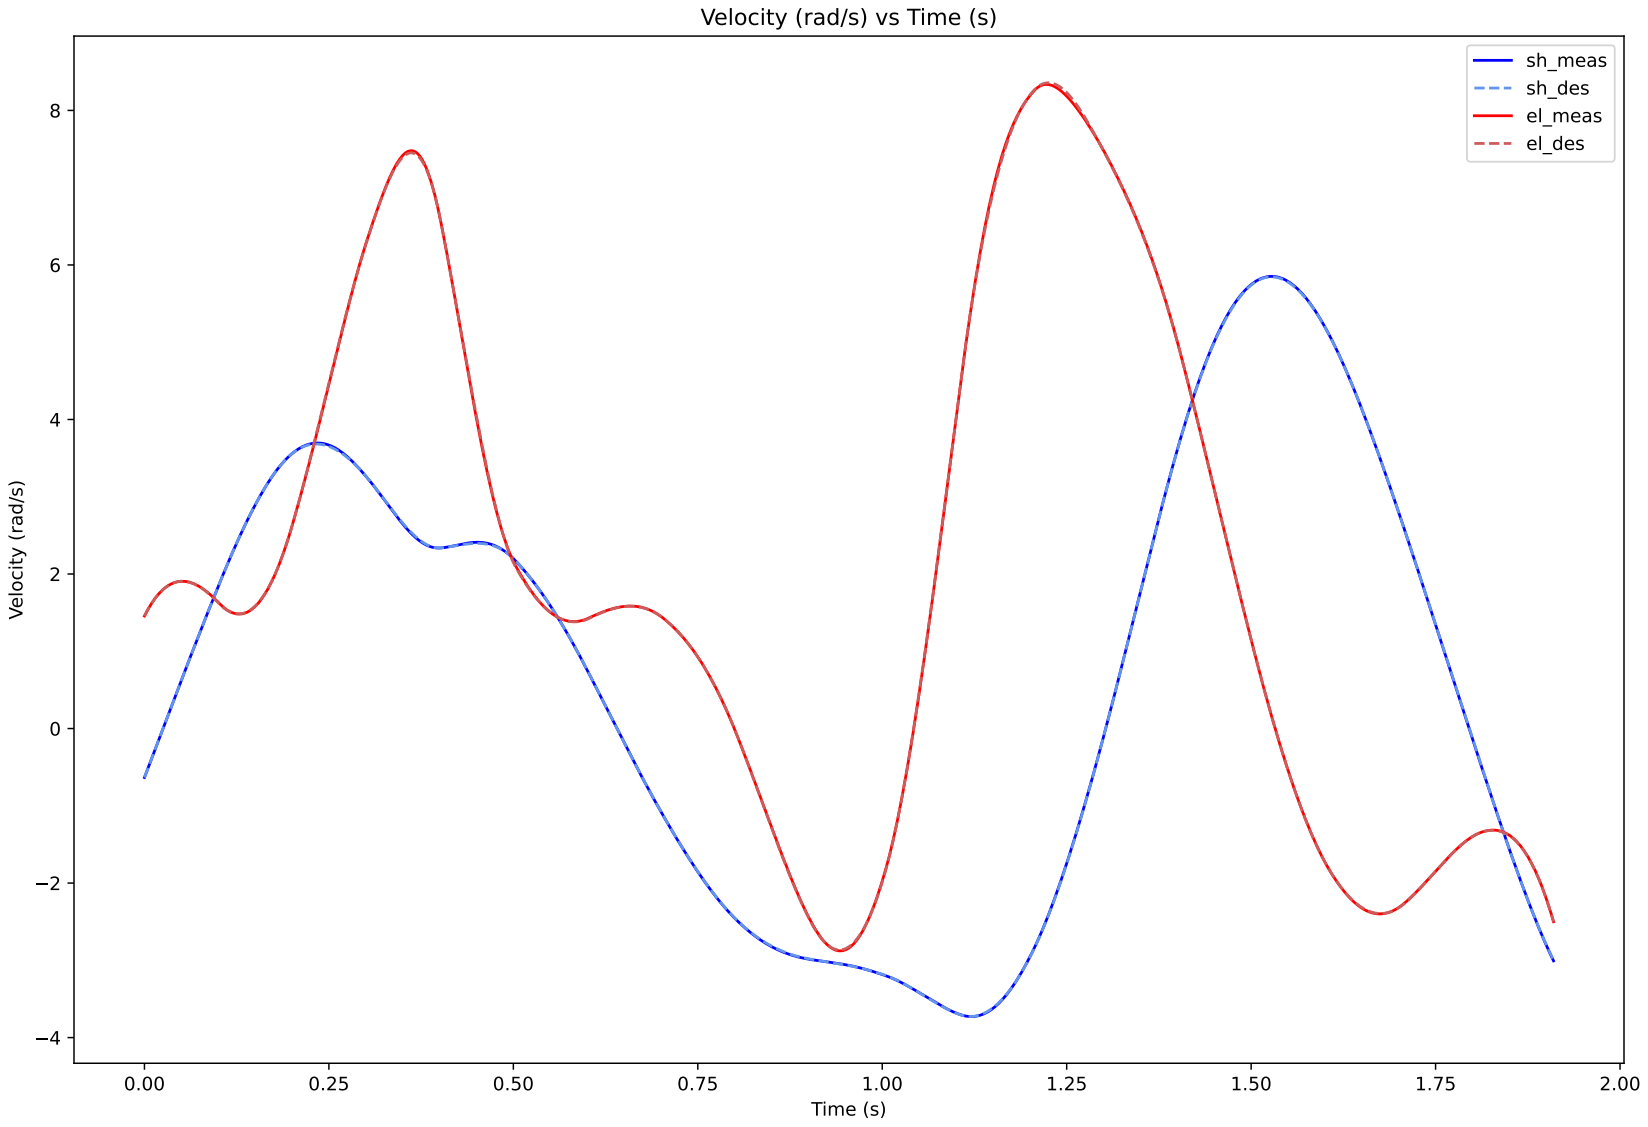
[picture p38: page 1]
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

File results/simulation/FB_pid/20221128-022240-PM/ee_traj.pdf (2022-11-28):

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

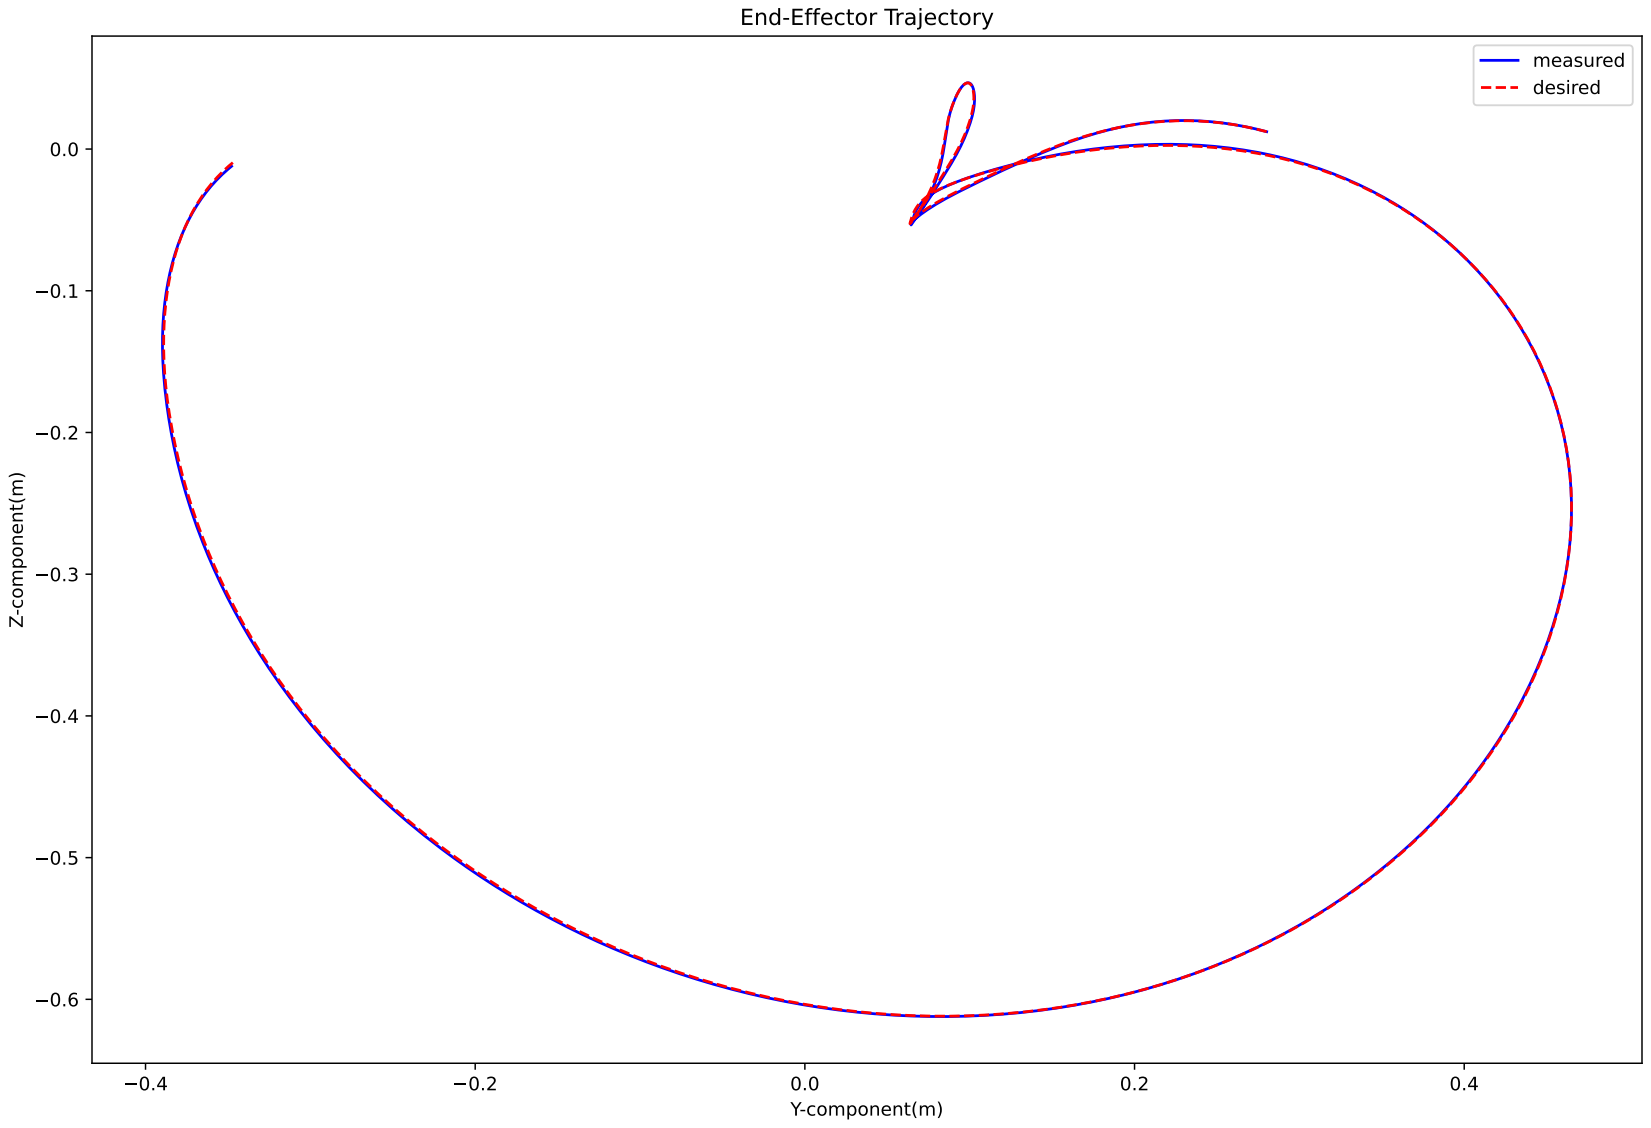
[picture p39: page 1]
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

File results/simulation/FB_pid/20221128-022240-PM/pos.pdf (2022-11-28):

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

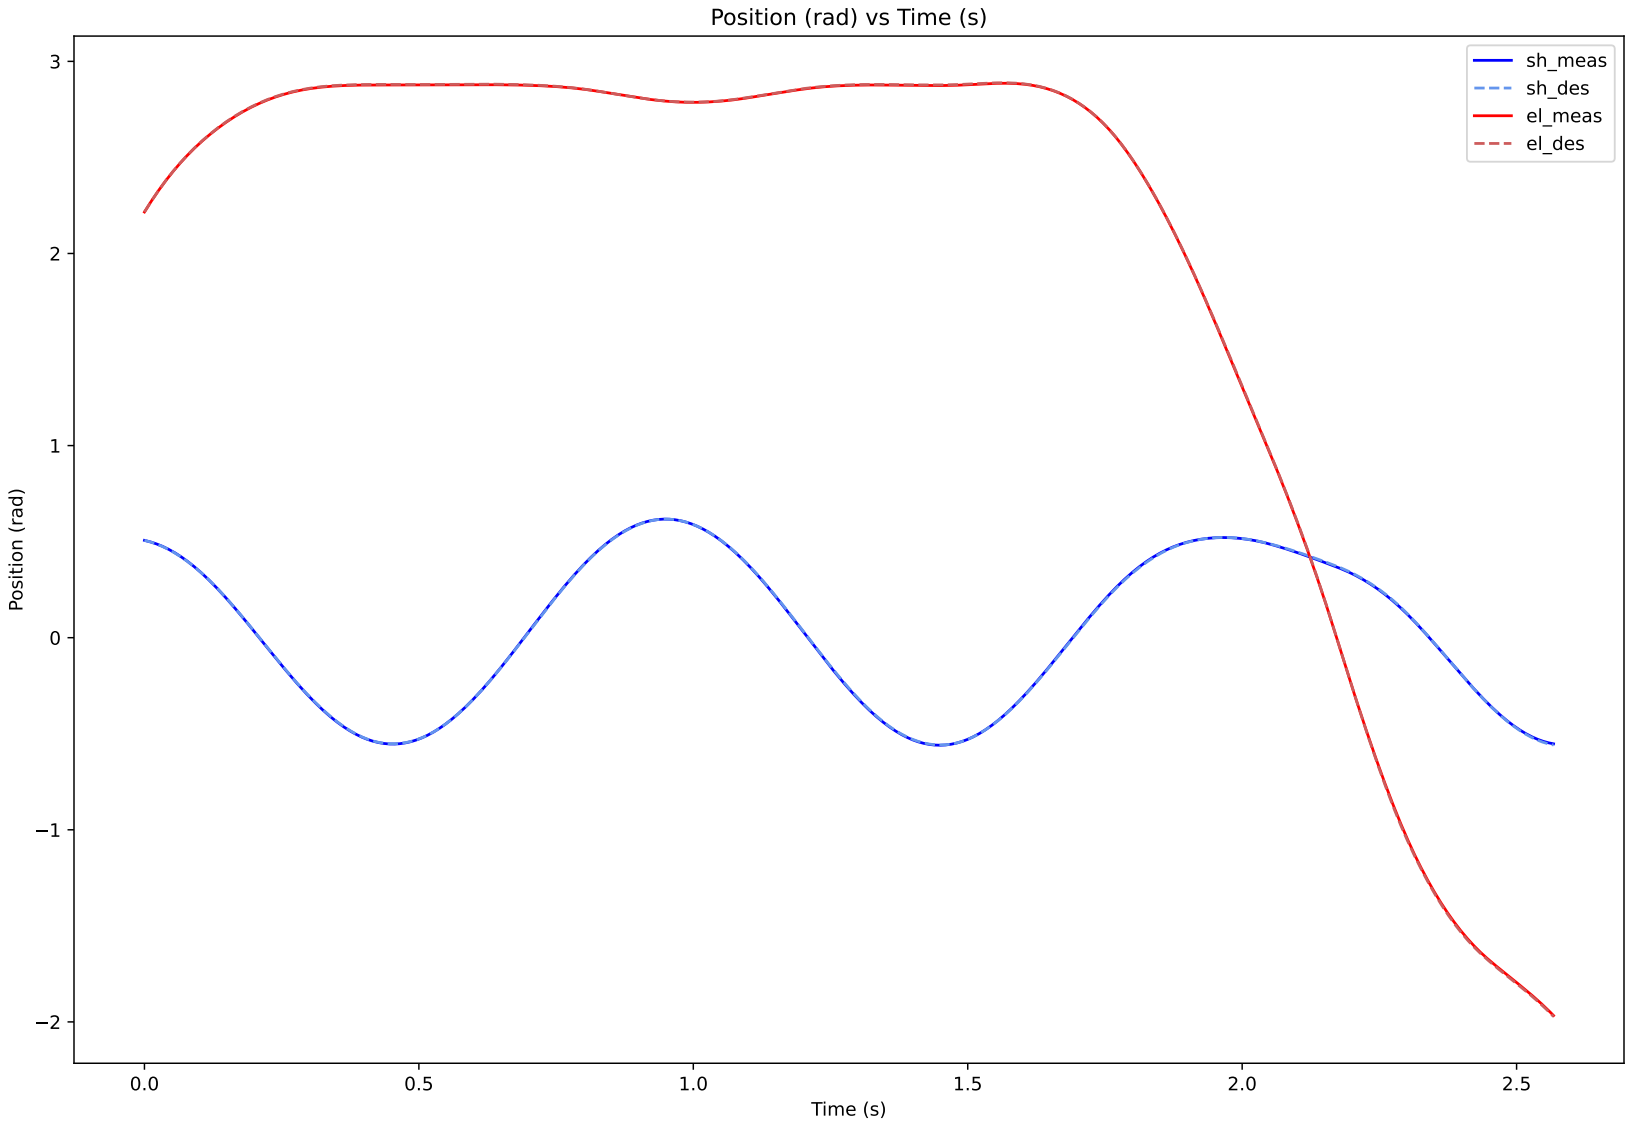
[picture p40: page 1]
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

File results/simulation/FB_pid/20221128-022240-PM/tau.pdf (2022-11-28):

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

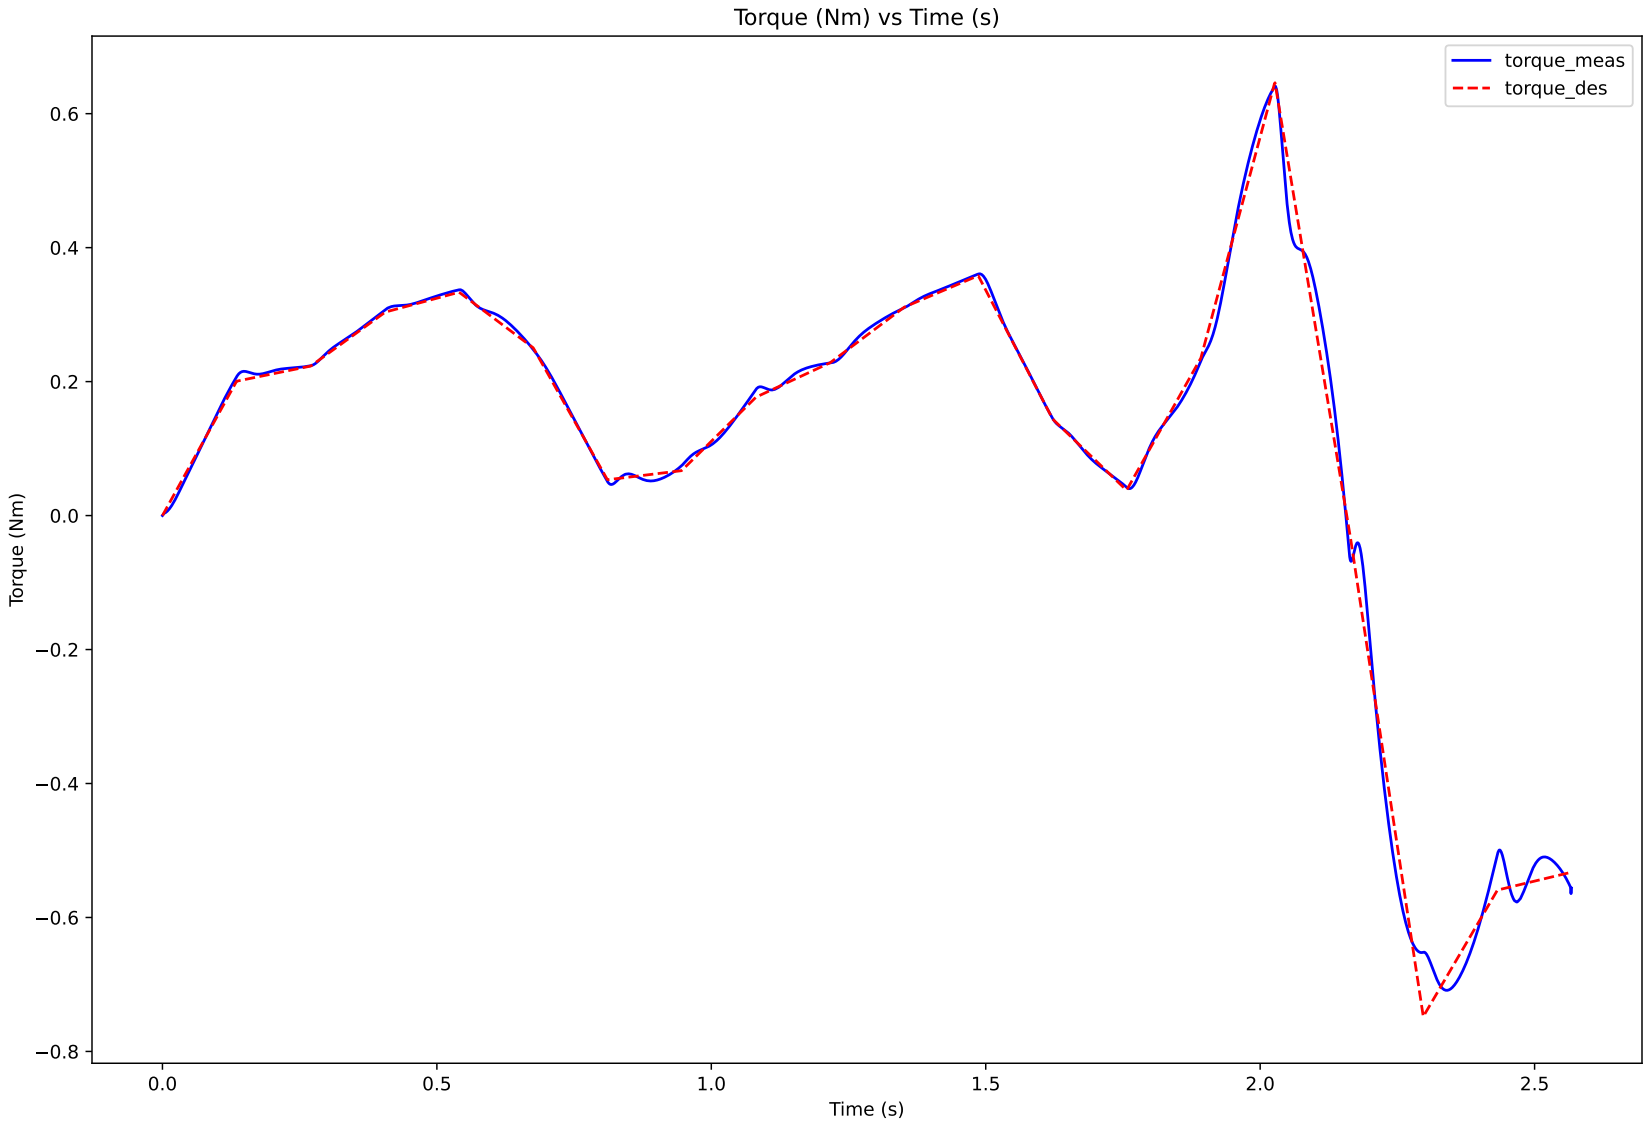
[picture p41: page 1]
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

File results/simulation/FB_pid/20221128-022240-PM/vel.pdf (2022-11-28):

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

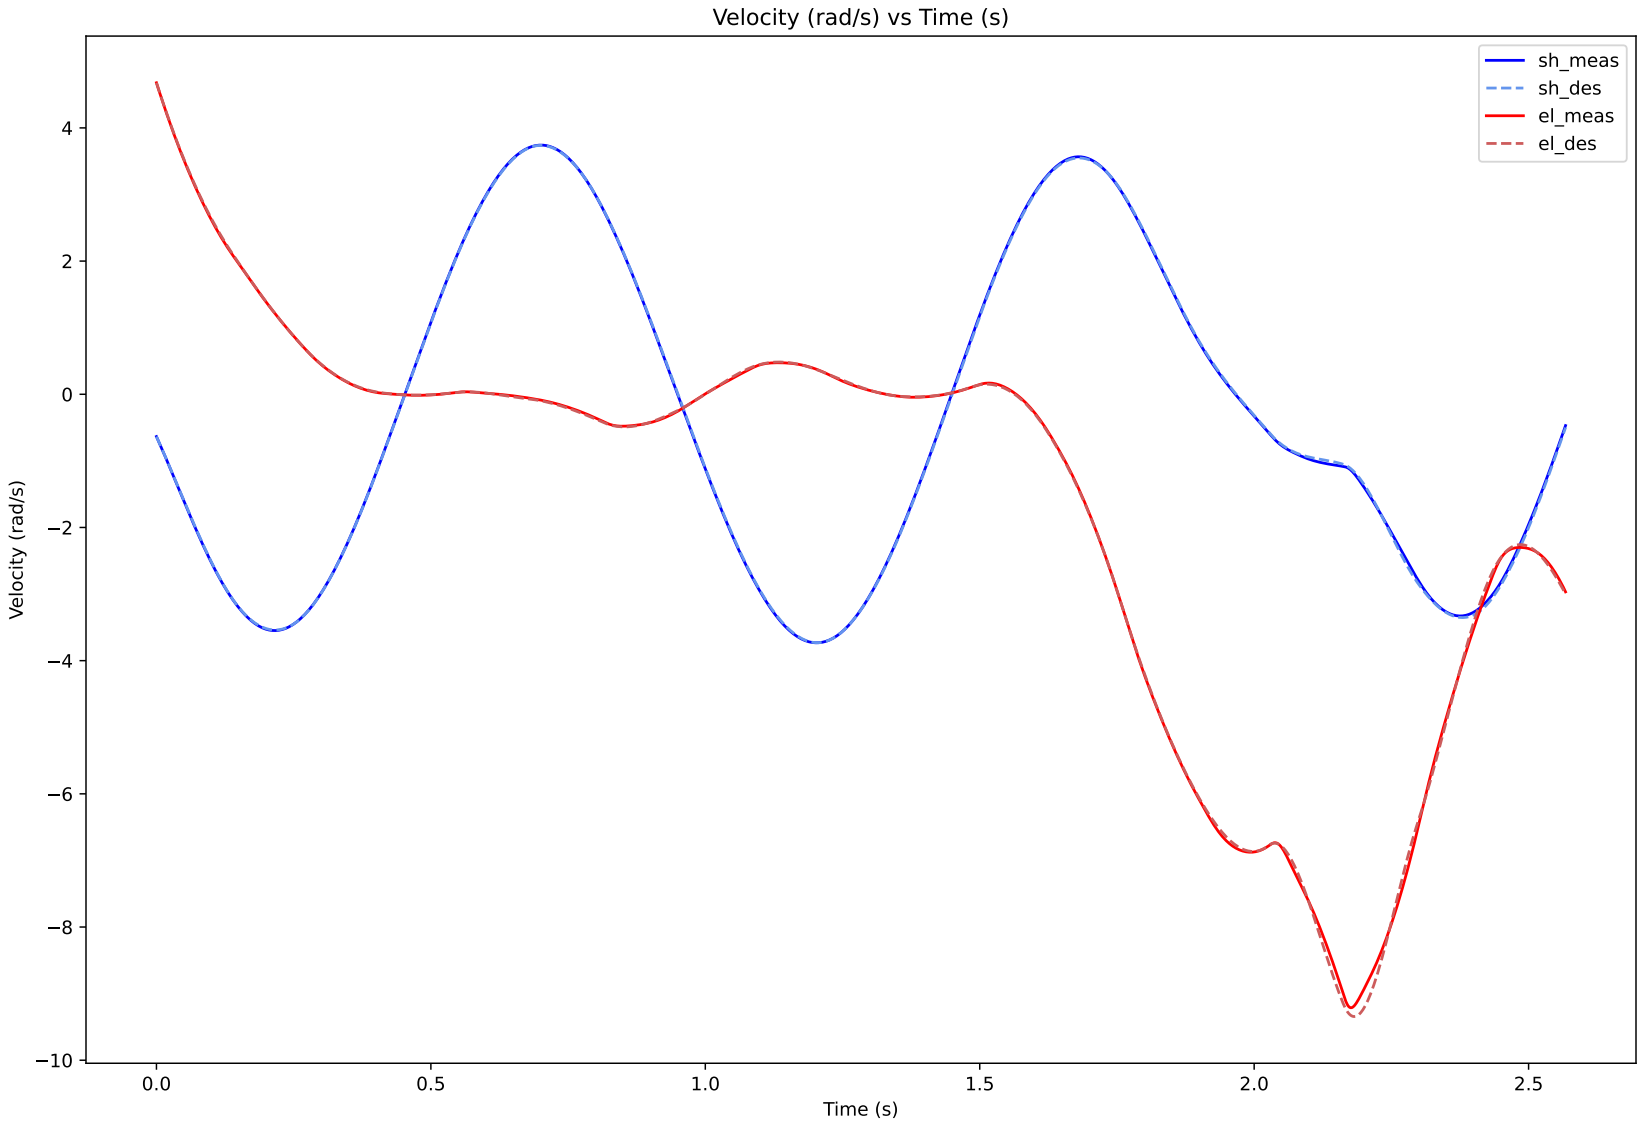
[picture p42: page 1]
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

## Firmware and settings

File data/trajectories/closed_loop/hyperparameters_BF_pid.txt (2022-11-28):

Kp=[100.]
Ki=[1.]
Kd=[2.]
Trajectory duration(seconds)=1.9098772981503944

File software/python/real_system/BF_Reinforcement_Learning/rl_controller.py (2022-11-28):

from abc import ABC, abstractmethod
import numpy as np
import os


class AbstractSwingController(ABC):
    @abstractmethod
    def __init__(self):
        self.controller_type = None

    @abstractmethod
    def get_control_command(self, meas_state, t, brach_state):
        tau_cmd = None
        kp_scale = None
        kd_scale = None
        des_traj_vals = None
        controller_specific_info = None

        return tau_cmd, des_traj_vals, kp_scale, kd_scale, controller_specific_info


class RLearningController(AbstractSwingController):
    def __init__(self, load_path='../src/reinforcement_learning/trained_controllers/Right_Left/', activation='tanh'):
        self.controller_type = 'rl'
        weights, biases = self._load_data(load_path)
        self.weights = weights
        self.biases = biases
        self.kp_scale = 0.0
        self.kd_scale = 0.0
        self.tau_scale = 1.0
        self.target_q = np.array([0.73, 1.97])
        self.target_dq = np.array([0.05, 0.05])
        self.switched_off_controller = False
        self.zero_offset_sh = np.deg2rad(0.0)  # We found out that the zero offset is actually not needed
        self.torque_scaler_odd = 0.90  # 0.92
        self.torque_scaler_even = 1.00  # 1.07
        self.des_traj_vals = {'el_des_pos': 0.0,
                              'el_des_vel': 0.0,
                              'sh_des_pos': np.NAN,
                              'sh_des_vel': np.NAN}

        self.expected_input_size = self.weights[0].shape[1]
        self.num_layers = len(self.weights)
        # self.last_obs = np.array([])
        if activation == 'tanh':
            self.activation = np.tanh
        else:
            raise NotImplementedError('Other activation functions than "tanh" not implemented yet')

    @staticmethod
    def _load_data(load_path='../src/reinforcement_learning/trained_controllers/Right_Left/'):
        weights = np.load(os.path.join(load_path, 'weights_2.npy'), allow_pickle=True)
        biases = np.load(os.path.join(load_path, 'biases_2.npy'), allow_pickle=True)

        return weights, biases

    def get_control_command(self, obs, t, brach_sign):
        # processing observation
        obs[0] += self.zero_offset_sh
        if brach_sign == -1:
            obs = np.multiply(obs, [[1], [-1], [1], [-1]])
        if len(obs) != self.expected_input_size:
            raise ValueError(f'the input you provided does not match '
                             f'the expected vector length {self.expected_input_size}')

        # if not self.switched_off_controller:
        scaler = np.array([3.14 / 2, 3.14 / 2, 4.0 / 2, 4.0 / 2])
        # scaler = np.array([3.14, 3.14, 4.0 / 2.0, 4.0 / 2.0])
        scaler = scaler[:, np.newaxis]
        scaled_obs = np.squeeze(obs * scaler)
        # scaled_obs = np.clip(scaled_obs, -1.0, 1.0)
        activation = np.tanh(np.dot(self.weights[0], scaled_obs) + self.biases[0])
        for n_layer in range(1, self.num_layers - 1):
            activation = np.tanh(np.dot(self.weights[n_layer], activation) + self.biases[n_layer])
        tau_cmd = np.dot(self.weights[-1], activation) + self.biases[-1]
        tau_cmd *= brach_sign
        if brach_sign == 1:
            tau_cmd *= self.torque_scaler_odd
        elif brach_sign == -1:
            tau_cmd *= self.torque_scaler_even
        '''
        else:
            tau_cmd = 0.0
            print(f'{obs} target configuration {self.target_q} with within error range {self.target_dq}, '
                  f'commanding torque {tau_cmd}')
        '''

        # post-processing torque command
        # tau_cmd = np.clip(tau_cmd, -1.0, 1.0)
        # tau_cmd *= self.tau_scale

        return tau_cmd, self.des_traj_vals, self.kp_scale, self.kd_scale, {}

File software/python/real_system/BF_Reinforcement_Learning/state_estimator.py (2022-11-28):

import numpy as np


class StateEstimator:
    def __init__(self, pr):
        self.pr = pr

    async def get_shoulder_state(self, brach_sign, th_2, th_2_vel):
        # brach_sign determines which arm is the support arm
        th_1 = None
        th_1_dot = None
        omega_x = None

        quat_wxyz, vel_xyz, acc_xyz, euler_xyz = await self.read_imu_data()

        th_imu = euler_xyz[0]
        omega_x, _, _ = np.deg2rad(vel_xyz)

        if brach_sign == 1:  # odd
            # get shoulder angle
            th_imu_0_to_2pi = th_imu + np.pi
            th_2_0_to_2pi = th_2 + np.pi
            th_1 = np.mod(np.pi - th_2_0_to_2pi + th_imu_0_to_2pi, 2 * np.pi) - np.pi

            # get shoulder velocity
            th_1_dot = omega_x - th_2_vel

        elif brach_sign == -1:  # even
            th_1 = self.wrap_pi2pi(np.pi - euler_xyz[0])
            th_1 *= -1.0
            th_1_dot = omega_x

        return th_1, th_1_dot, th_imu, omega_x

    async def read_imu_data(self):
        imu = await self.pr.cycle([], request_attitude=True)
        imu_data = imu[0]
        quat_wxyz = (
            imu_data.attitude.w,
            imu_data.attitude.x,
            imu_data.attitude.y,
            imu_data.attitude.z,
        )
        vel_xyz = imu_data.rate_dps.x, imu_data.rate_dps.y, imu_data.rate_dps.z
        acc_xyz = (
            imu_data.accel_mps2.x,
            imu_data.accel_mps2.y,
            imu_data.accel_mps2.z,
        )
        euler_xyz = (
            imu_data.euler_rad.roll,
            imu_data.euler_rad.pitch,
            imu_data.euler_rad.yaw,
        )
        return quat_wxyz, vel_xyz, acc_xyz, euler_xyz

    @staticmethod
    def wrap_pi2pi(x):
        # wrapping x to [-pi, pi]
        angle = x % (2 * np.pi)
        if angle > np.pi:
            angle -= 2 * np.pi
        return angle

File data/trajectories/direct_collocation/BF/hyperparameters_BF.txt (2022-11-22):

n=20
tau_limit=3.0
initial_state=(-0.631562, -1.872709, -0.633643, 1.456502)
theta_limit=[2.0943951023931953, 2.8797932657906435]
speed_limit=10
ladder_distance=0.34
final_state=(0.6806784082777885, 1.9198621771937625, -3.0, -2.5)
R=100
time_panalization=50
init_guess=[0.0, 2.0]
max_timestep=0.8
min_timestep=0.1

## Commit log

2022-11-16 initial push for rl, will not work yet
    [Base.STL, IMU.STL, acromonk_mujoco.xml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]
2022-11-18 raspberry pi setup added
2022-11-19 first version of the testbench description added. CAD assembly video needs to be added
2022-11-20 hook --> gripper
2022-11-20 raspberry pi remote access guide added
2022-11-21 BOM added
2022-11-21 sensor reading added
2022-11-21 3d printing cost needs to be added
2022-11-21 figure with gripper ROA moved to trajectory optimization readme
2022-11-21 pid README added
2022-11-21 3D printing materials added
2022-11-22 urdf_files added
    [Base.STL, Base.obj, IMU.STL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]
2022-11-22 hyper parameters and csv files the atomic behavior addded
    [BF.csv, FB.csv, ZB.csv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]
2022-11-24 closed_loop_control trajectories/hyper parameters with tvlqr added
    [BF.csv, FB.csv, ZB.csv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]
2022-11-24 traj_stabilization.py:script for trajectory stabilization using PID and TVLQR
2022-11-24 closed-loop control with PID in simulation added
2022-11-24 stabilzer mergerd for pid and tvlqr controller
2022-11-25 first version of simulation package tested
    [BF.csv, FB.csv, ZB.csv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]
2022-11-28 reinforcement_learning_controller.py:added rl controller for the code
    [reinforcement_learning_controller.py]
2022-11-28 results,trajectories and hyperparameters added
    [BF_pid.csv, BF_traj.csv, BF_tvlqr.csv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]
2022-11-28 meshes and urdf files merged in one folder and scripts modified for relative paths
    [Base.STL, Base.obj, IMU.STL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]
2022-11-28 CAD file added
2022-11-28 FB real system code added
    [LR_v2_Sept1_1000Hz.csv, RL_PD.csv]
2022-12-01 results for real_time experiments added
    [BF_pd_5x.csv, BF_rl_5x.csv, BF_tvlqr_1x.csv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]
2023-04-17 gripper related analysis added
